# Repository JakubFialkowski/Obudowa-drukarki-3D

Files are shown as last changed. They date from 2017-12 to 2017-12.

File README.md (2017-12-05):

<h1># Obudowa drukarki 3D</h1>
Zamknięta obudowa dla drukarki 3D z funkcją utrzymywania zadanej temperatury.

<p>-komora podzielona na dwie strefy za pomoca wysuwanego blatu<br>
- cztery punkty pomiaru temperatury<br>
- utrzymywanie zadanej temperatury za pomocą wentylatorów i rególatorów PID<br>
- wyświetlanie parametrów oraz konfiguracja ustawień za pomocą wyświetlacza LCD oraz 4 przycisków<br>
- uchwyt szpuli filamentu pozwalający na pomiar wagi pozsotałego materiału
  
  <b>Szczegółowy opis w pliku "Projekt i wykonanie zamkniętej komory przeznaczonej do pracy drukarki 3d.pdf" </b>

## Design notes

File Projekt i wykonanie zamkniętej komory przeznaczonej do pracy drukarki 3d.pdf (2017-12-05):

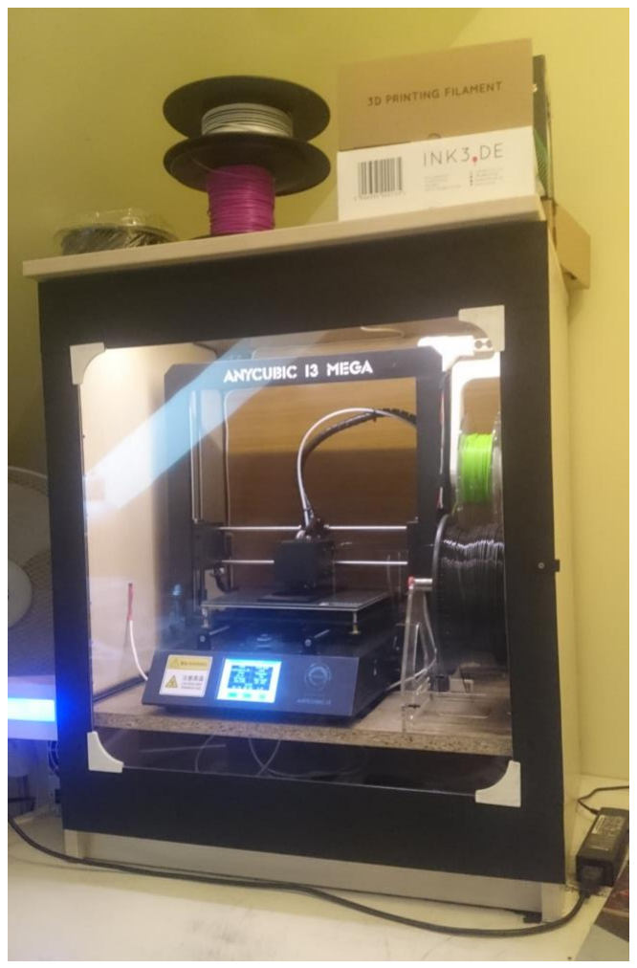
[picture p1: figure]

## Projekt i wykonanie zamkniętej komory przeznaczonej do pracy

drukarki 3d.

Cel:
Budowa zamkniętej komory pozwalającej na pracę drukarki 3d.

Wymagania projektowe:
- Zamknięta komora, redukująca hałas wytwarzany podczas pracy drukarki, osiadanie kurzu na elementy mechaniczne drukarki.
- Regulacja temperatury wewnątrz komory
- Swobodny dostęp do drukarki

Zalety zamkniętej obudowy:
- Zmniejszenie poziomu hałasu
- Zmniejszenie ilości kurzu domowego osiadającego na częściach mechanicznych drukarki.
- Utrzymywanie odpowiedniej temperatury w obrębie wydruku (konieczne przy niektórych materiałach technologii FDM)

Budowa komory:
Komora zbudowana jest w formie prostopadłościanu o wymiarach 60cm x 67cm x 44cm. Dostęp do komory realizowany jest za pomocą drzwi wykonanych z przezroczystego pleksiglasu, umożliwiającego podgląd pracy drukarki.

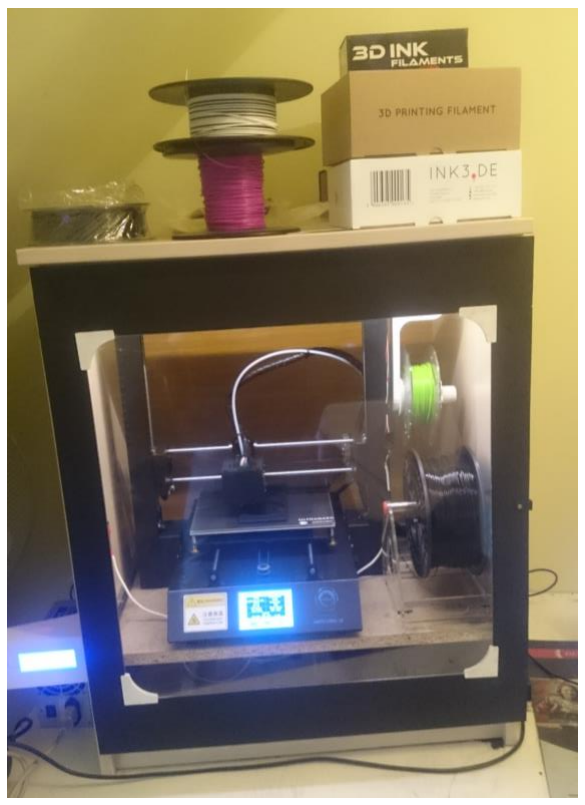
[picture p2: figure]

Rys.1. Zamknięta komora

Drukarka umieszczona wewnątrz komory postawiona została na wysuwanym blacie, który umożliwia wysunięcie urządzenia z komory w celach serwisowych.

Dodatkowo blat rozdziela wnętrze komory na dwie strefy:

- strefę wydruku
- strefę w której pracuje elektronika drukarki

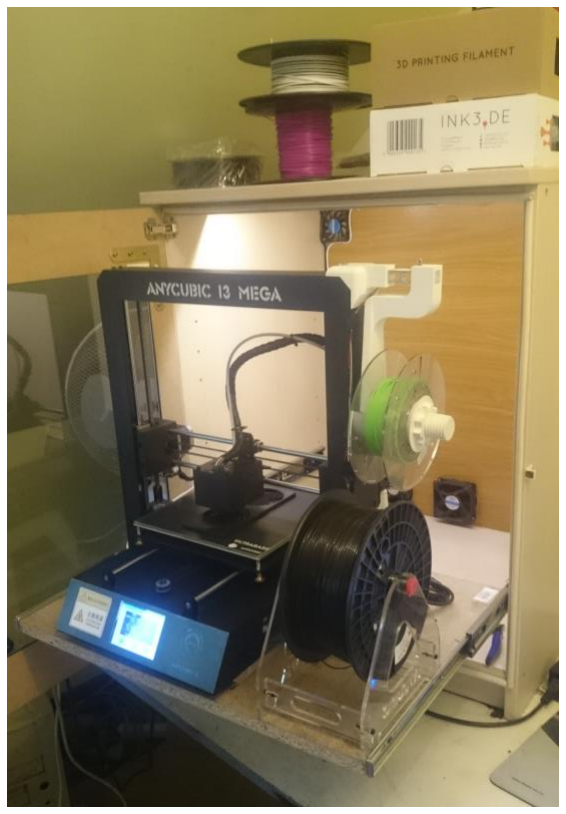
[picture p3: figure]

Rys.2. Drukarka wysunięta w celach serwisowych

Komora wyposażona została w uszczelki okienne na łączeniu komory z drzwiami, dodatkowo domknięcie drzwi za pomocą magnesów neodymowych pozwala na odpowiednie uszczelnienie komory.

Utrzymywanie temperatury wewnątrz komory:
W celu utrzymania odpowiedniej temperatury wewnątrz drukarki zaprojektowana system automatycznej kontroli temperatury.

System składa się z:

- Czujników temperatury
- Wentylatorów
- Mikrokontrolera pozwalającego na odczyt temperatury i odpowiednie wysterowanie pracą wentylatorów.

Pomiar temperatury odbywa się za pomocą dwóch czujników cyfrowych DS18B20 oraz jednego AM2320.

Regulacja temperatury odbywa się za pomocą:

- Dwóch wentylatorów 6010 dla strefy wydruku
- Dwóch wentylatorów o średnicy 100mm dla strefy elektroniki

Jako mikrokontroler zastosowano Arduino Uno.

Wykorzystane elementy:
- 3x DS18B20
- AM2320
- Arduino Uno
- Lcd 4x20
- 4x tact switch
- przekaźnik 10A 250VAC
- mostek H, układ L293D
- konwenter ADC HX711
- belka tensometryczna NA27
- 2x wentylator 6010
- 2x wentylator o średnicy 100mm
- Pasek led o długości 55cm

Funkcjonalność:

- Pomiar temperatury w trzech punktach komory, dodatkowo odczyt temperatury na zewnątrz komory.
- Pomiar wilgotności panującej w komorze
- Pomiar wagi filamentu pozostałego na szpuli.
- Wyświetlanie danych pomiarowych
- Wprowadzanie danych dotyczących zadanej temperatury
- Sterowanie oświetleniem komory

Działanie programu:

### 1. Menu

Użytkownik posiada do dyspozycji wyświetlacz LCD z wbudowanym menu, pozwalającym na wyświetlanie pomiarów, wprowadzenie zadanych wartości temperatur oraz wysterowanie oświetleniem. Do nawigacji wykorzystano 4 przyciski.

Ekran POMIARY wyświetla dane z dostępnych czujników w celu prezentacji użytkownikowi, wyświetlane są od lewej:

- Zadane temperatury
- Temperatury wewnątrz komory
- Wilgotność
- Temperatura zewnętrzna
- Waga filamentu

Poruszając się po menu, mamy do dyspozycji następujące pozycje:

- Ustaw czas druku (w rozwoju)
- Ustaw temperaturę góra ( wartość temperatury dla górnego czujnika)
- Ustaw temperaturę środek ( wartość temperatury dla srodkowego czujnika)
- Ustaw temperaturę dół ( wartość temperatury dla dolnego czujnika)
- Oświetlenie LED ( pozwala sterować oświetleniem komory)

### 2. Regulacja temperatury

Regulacja temperatury odbywa się za pomocą programowych regulatorów PID. Wzrost temperatury w komorze powodowany jest przez podgrzewany stół oraz głowice drukującą. Stół ma powierzchnię 0,0441 m²

co przy jego temperaturze 60 oC podnosi temperaturę wnętrza komory o około 10 oC w czasie 1h. W regulacji istotne jest niedopuszczenie do przekroczenia zadanej temperatury.

Wartością wejściową jest wartość temperatury konkretnego czujnika, wartość zadana jest ustala przez użytkownika poprzez odpowiedni ekran menu. Wartością wyjściowa jest sygnał PWM służący do wysterowania prędkością obrotowa wentylatorów poprzez układ mostka H. Wentylatory zasilane są za pomocą L293D zasilanego napięciem 12V. Mostek H pozwala na płynną regulację prędkości obrotowej wentylatorów.

Nastawy regulatorów zostały dobrane eksperymentalnie, obserwując zmianę wartości temperatur.

### 3. Pomiar wagi filamentu

W celu pomiaru wagi filamentu pozostałego na szpuli zaprojektowano uchwyt na szpule, wyposażony w belkę tensometryczna NA27 posiadającą zakres pomiarowy od 0-5kg. W celu pomiaru wartości nacisku na belce tensometrycznej wykorzystano moduł HX711 będący wzmacniaczem operacyjnym wyposażonym w 24-bitowy konwerter ADC. Części uchwytów zostały wydrukowane z materiału PLA.

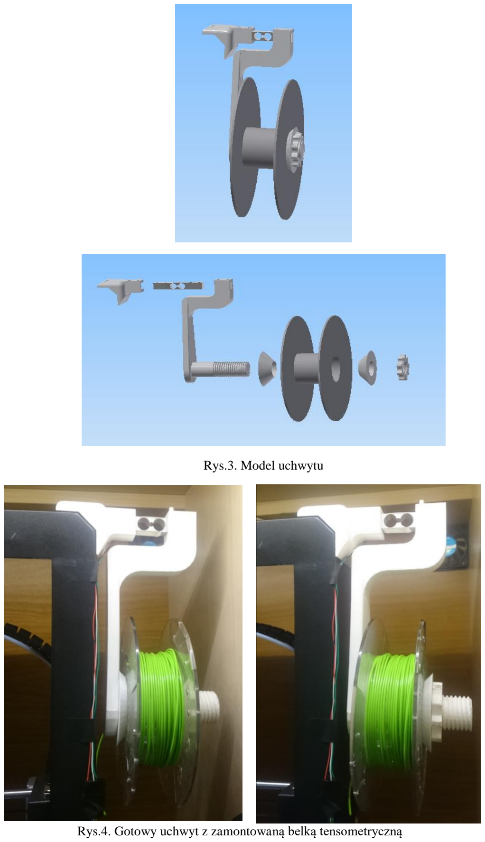
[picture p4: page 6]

Rys.3. Model uchwytu

Rys.4. Gotowy uchwyt z zamontowaną belką tensometryczną

### 4. Wyświetlacz

Wyświetlacz obsługiwany jest za pomocą komunikacji I²C (TWI) poprzez moduł PCF8574. W celu obsługi menu wykorzystywane są 4 przyciski typu tact. Wydrukowano także obudowę wyświetlacza pozwalającą na montaż przycisków.

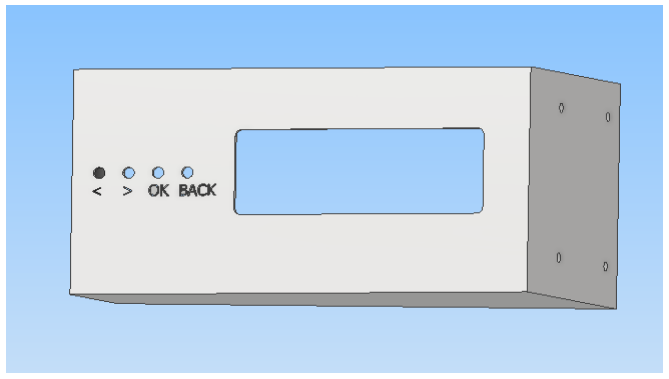
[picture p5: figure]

Rys.5. Model obudowy wyświetlacza

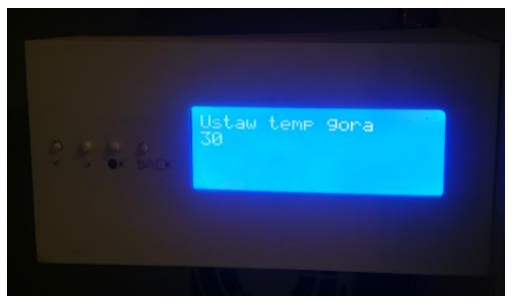
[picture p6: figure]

Rys.6. Dostępne ekrany MENU

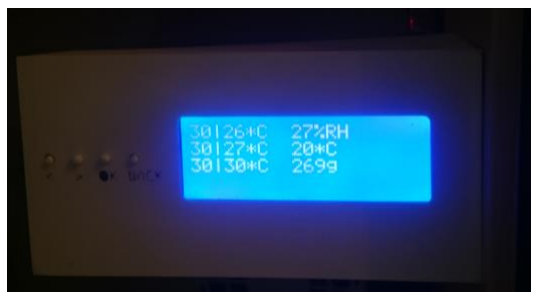
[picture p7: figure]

### 5. Zasilanie

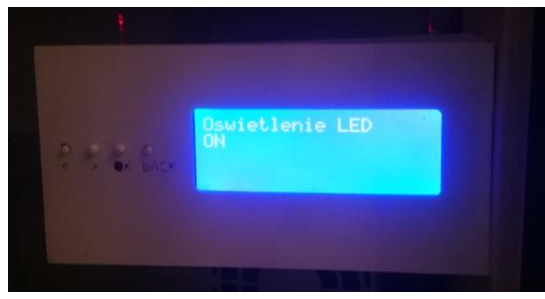
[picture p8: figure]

Do zasilenia mikrokontroler, oświetlenia led, wentylatorów, wyświetlacza wykorzystano komputerowy zasilacz ATX, dostarczający napięcie 12V oraz 5V.

Dalsze plany rozwojowe:

- Wygłuszenie komory za pomocą pianki ognioodpornej
- Zastosowanie czujników dymu, płomienia wewnątrz komory, które pozwolą na awaryjne wyłączenie drukarki w przypadku wystąpienia ognia.
- Zastosowanie filtrów przeciwpyłowych na wentylatorach

- Budowa wyciągu oparów, podłączonego do wentylacji mieszkania
- Zastosowanie komputera Raspberry PI wraz z oprogramowaniem Octoprint w celu sterowania zdalnego parametrami druku
- Wyposażenie Raspberry PI w kamerę internetową w celu zdalnego monitoringu.

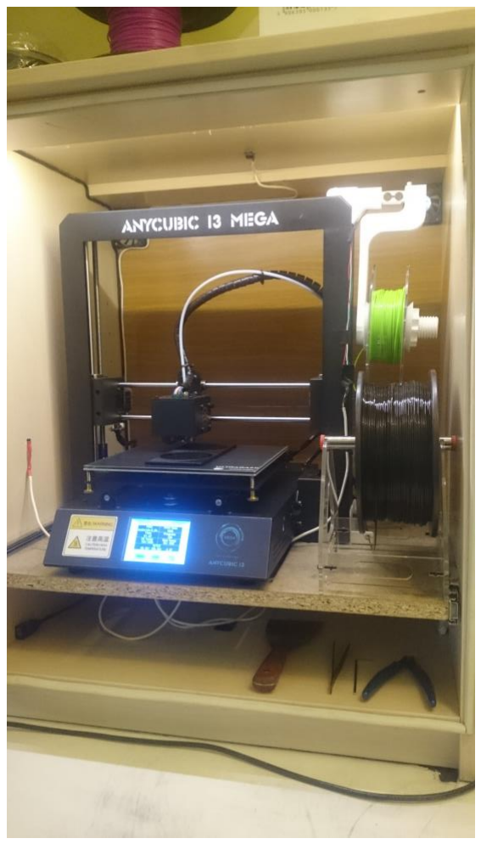
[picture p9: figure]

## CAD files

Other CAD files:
belka_tensometryczna.ipt
mocowanie_do_ramy.ipt
nakretka.ipt
stożek.ipt
szpula.ipt
uchwyt_filamentu.ipt
zlozenie.iam

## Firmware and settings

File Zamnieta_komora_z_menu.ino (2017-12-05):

#include <Wire.h>
#include <LiquidCrystal_I2C.h> 
#include <OneWire.h>
#include <DS18B20.h>
#include <AM2320.h>
#include "HX711.h"
#include <PID_v1.h>
AM2320 th;


LiquidCrystal_I2C lcd(0x27, 2, 1, 0, 4, 5, 6, 7, 3, POSITIVE); //definicja wyświetlacza
// definicja przycisków
#define BTN_BACK  11
#define BTN_NEXT  10
#define BTN_PREV  8
#define BTN_OK    9

#define ONEWIRE_PIN 4 // czujnik temp 18b20
#define SENSORS_NUM 3 // ilosc czujnikow 18b20

#define calibration_factor -2400 //Wartosc uzyskana za pomoca SparkFun_HX711_Calibration sketch
#define zero_factor 9959920//16180400 //wartosc uzyska za pomoca SparkFun_HX711_Calibration sketch

//definicja pinow dla HX711
#define DOUT  3
#define CLK  2

HX711 scale(DOUT, CLK);

// Adresy czujnikow DS18B20 dla magistrali one wire
const byte address[SENSORS_NUM][8] PROGMEM = {
  0x28, 0xAC, 0x71, 0x7B, 0x5, 0x0, 0x0, 0x96,
0x28, 0x61, 0x64, 0x11, 0xA9, 0x88, 0x81, 0xA0,
0x28, 0x61, 0x64, 0x11, 0xA9, 0xB7, 0x74, 0xDE
};
OneWire onewire(ONEWIRE_PIN);
DS18B20 sensors(&onewire);
int czujnik[3];
float czujnikAM[2];
//zmienne dla regulatorow PID
 int wentylator_gora = 6;
int wentylator_dol = 12;
 double Setpoint, Input, Output;
 double Setpoint1, Input1, Output1;

//Nastawy regulatorow PID
double Kp=80, Ki=5, Kd=1;
PID myPID(&Input, &Output, &Setpoint, Kp, Ki, Kd, REVERSE);

double Kp1=80, Ki1=5, Kd1=1;
PID myPID1(&Input1, &Output1, &Setpoint1, Kp1, Ki1, Kd1, REVERSE);

//struktura danych dla menu
typedef struct {
  String label;
  int minVal;
  int maxVal;
  int currentVal;
  void (*handler)();
} STRUCT_MENUPOS;

typedef enum {
  BACK, NEXT, PREV, OK, NONE
} ENUM_BUTTON;

STRUCT_MENUPOS menu[6]; //liczba pozycji menu

int currentMenuPos = 0;
int menuSize;
bool isInLowerLevel = false;
int tempVal;

void setup() {
  
  Serial.begin(9600);
  lcd.begin(20, 4);
  lcd.setBacklight(255);
  sensors.begin();
  sensors.request();
  scale.set_scale(calibration_factor); //ustawienie wagi na 0
  scale.set_offset(zero_factor); //ustawienie wagi na 0 przy znanej wartosci

  pinMode(5, OUTPUT);
  pinMode(BTN_NEXT, INPUT_PULLUP);
  pinMode(BTN_PREV, INPUT_PULLUP);
  pinMode(BTN_BACK, INPUT_PULLUP);
  pinMode(BTN_OK, INPUT_PULLUP);
  pinMode(wentylator_gora, OUTPUT);
  //Wejscie i wartosc zadana dla PID
  Input = (czujnikAM[1]+czujnik[2])/2; //srednia z dwoch czujnikow wewnatrz strefy wydruku
  Setpoint = (menu[2].currentVal + menu[4].currentVal)/2 ; 

  Input1 = czujnik[1]; 
  Setpoint1 = menu[3].currentVal;
  //wlaczenie PIDow w trybie automatycznym
  myPID.SetMode(AUTOMATIC);
  myPID1.SetMode(AUTOMATIC);
  //definicja Menu
  menu[0] = {"Parametry", 0, 1, 5, parametry};
  menu[1] = {"Oswietlenie LED", 0, 1, 0, oswietlenieLed};
  menu[2] = {"Ustaw temp srodek ", 0, 100, 30, NULL};
  menu[3] = {"Ustaw temp dol", 0, 100, 30, NULL};
  menu[4] = {"Ustaw temp gora", 0, 100, 30, NULL};
  menu[5] = {"Ustaw czas druku", 0, 100, 40, NULL};
  menuSize = sizeof(menu)/sizeof(STRUCT_MENUPOS);
}

void loop() {
  drawMenu();
  if(currentMenuPos == 0) {
    parametry();
  }
  Input = (czujnikAM[1]+czujnik[0])/2;
  Setpoint = (menu[2].currentVal + menu[4].currentVal)/2 ;
  Input1 = czujnik[1];
  Setpoint1 = menu[3].currentVal;
  //Obliczenie PIDow
  myPID.Compute();
  myPID1.Compute();
  //Ograniczenie sygnału PWM wysterowania ( przy małych prędkościach obrotowych wentylatory wydają piskliwe dzwięki)
  if (Output >= 130){
    analogWrite(wentylator_gora,Output);
  }
  else
  {
    analogWrite(wentylator_gora,0);
  }
  if (Output1 >= 130){
    analogWrite(wentylator_dol,Output1);
  }
    else
  {
    analogWrite(wentylator_dol,0);
  }
  //wyswietlanie wartosci regulatorow PID za pomoca portu szeregowego ( w celach diagnostycznych)
  Serial.print(Input);
  Serial.print("  ");
  Serial.print(Setpoint);
  Serial.print("  ");
  Serial.print(Output);
  Serial.print("            ");
  Serial.print(Input1);
  Serial.print("  ");
  Serial.print(Setpoint1);
  Serial.print("  ");
  Serial.println(Output1);

  delay(100);
}
  
ENUM_BUTTON getButton() {
  if(!digitalRead(BTN_BACK)) return BACK;
  if(!digitalRead(BTN_NEXT)) return NEXT;
  if(!digitalRead(BTN_PREV)) return PREV;
  if(!digitalRead(BTN_OK)) return OK;
  return NONE;
}

void drawMenu() {
  //odczyt z czujnika AM2320
  th.Read();
  czujnikAM[0]=th.h;
  czujnikAM[1]=th.t;
  
  for (byte i=0; i<SENSORS_NUM; i++){
    czujnik[i]=sensors.readTemperature(FA(address[i]));
  }
  sensors.request();
    
  static unsigned long lastRead = 0;
  static ENUM_BUTTON lastPressedButton = OK;
  static unsigned int isPressedSince = 0;
  int autoSwitchTime = 500;

  ENUM_BUTTON pressedButton = getButton();

  if(pressedButton == NONE && lastRead != 0) {
    isPressedSince = 0;
    return;
  }
  if(pressedButton != lastPressedButton) {
    isPressedSince = 0;
  }

  if(isPressedSince > 3) autoSwitchTime = 70;
  if(lastRead != 0 && millis() - lastRead < autoSwitchTime && pressedButton == lastPressedButton) return;

  isPressedSince++;
  lastRead = millis();
  lastPressedButton = pressedButton;
  
  switch(pressedButton) {
    case NEXT: handleNext(); break;
    case PREV: handlePrev(); break;
    case BACK: handleBack(); break;
    case OK: handleOk(); break;
  }

  lcd.home();
  lcd.clear();
  if(isInLowerLevel && currentMenuPos != 0  ) {
  lcd.print(menu[currentMenuPos].label);
  
    if(menu[currentMenuPos].handler != NULL) {
      (*(menu[currentMenuPos].handler))();
    } else {
      lcd.setCursor(0, 1);
      lcd.print(tempVal);
    }
  } else if (currentMenuPos != 0) {
    lcd.print(menu[currentMenuPos].label);
  }
  
}

void handleNext() {
  if(isInLowerLevel) {
    tempVal++;
    if(tempVal > menu[currentMenuPos].maxVal) tempVal = menu[currentMenuPos].maxVal;
  } else {
    currentMenuPos = (currentMenuPos + 1) % menuSize;
  }
}

void handlePrev() {
  if(isInLowerLevel) {
    tempVal--;
    if(tempVal < menu[currentMenuPos].minVal) tempVal = menu[currentMenuPos].minVal;
  } else {
    currentMenuPos--;
    if(currentMenuPos < 0) currentMenuPos = menuSize - 1;
  }
}

void handleBack() {
  if(isInLowerLevel) {
    isInLowerLevel = false;
  }
}

void handleOk() {
  if(menu[currentMenuPos].handler != NULL && menu[currentMenuPos].maxVal <= menu[currentMenuPos].minVal) {
    (*(menu[currentMenuPos].handler))();
    return;
  }
  if(isInLowerLevel) {
    menu[currentMenuPos].currentVal = tempVal;
    isInLowerLevel = false;
  } else {
    tempVal = menu[currentMenuPos].currentVal;
    isInLowerLevel = true;
  }
}

void parametry() {
  
  
  lcd.setCursor(0,0);
  lcd.print(menu[2].currentVal);
  lcd.print("|");
  lcd.print(czujnik[0]);
  lcd.setCursor(5,0);
  lcd.print("*C");
  lcd.setCursor(0,2);
  lcd.print(menu[3].currentVal);
  lcd.print("|");
  lcd.print(czujnik[1]);
  lcd.setCursor(5,2);
  lcd.print("*C");
  lcd.setCursor(0,1);
  lcd.print(menu[4].currentVal);
  lcd.print("|");
  lcd.print(czujnikAM[1],0);
  lcd.setCursor(5,1);
  lcd.print("*C");
  lcd.setCursor(9,0);
  lcd.print(czujnikAM[0],0);
  lcd.setCursor(11,0);
  lcd.print("%RH");
  lcd.setCursor(9,1);
  lcd.print(czujnik[2]);
  lcd.setCursor(11,1);
  lcd.print("*C");
  lcd.setCursor(9,2);
  lcd.print(-scale.get_units(), 0);
 // lcd.setCursor(14,2);
  lcd.print("g");
  
  
}

void oswietlenieLed() {
  String dictonary[] = {"ON", "OFF"};
  lcd.setCursor(0,1);
  lcd.print(dictonary[tempVal]);
  if (dictonary[tempVal] == "OFF"){
    digitalWrite(5, HIGH);
  }
    else
    {
      digitalWrite(5, LOW);
    }
  
}
